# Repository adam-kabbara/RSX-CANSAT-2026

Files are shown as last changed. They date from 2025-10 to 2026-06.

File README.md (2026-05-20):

# RSX CanSat 2T5-2T6 Designs 

<div align="left">
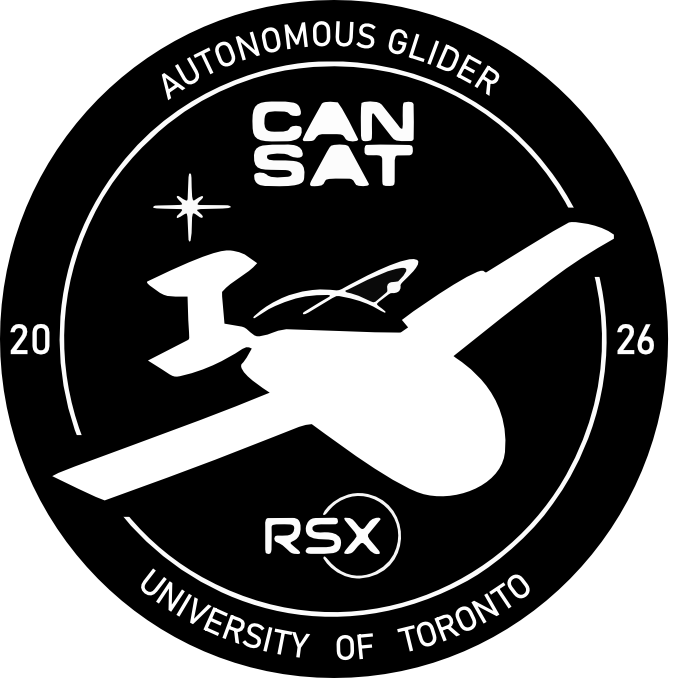
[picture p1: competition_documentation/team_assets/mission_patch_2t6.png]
mission_patch
    
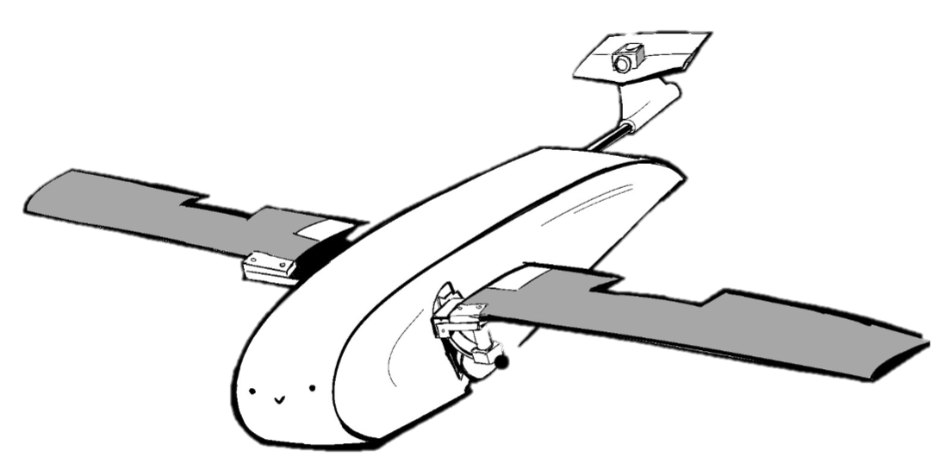
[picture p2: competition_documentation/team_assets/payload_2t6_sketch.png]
payload_sketch
    
    mascot_capybara
</div>
<br>

This repository contains all files created by the Aerial Team of Robotics for Space eXploration (RSX) at the University of Toronto, supporting our entry in the 2026 CanSat Competition.

**Competition Team Members:**
<table align="left">
    <tr><td align="center">Adam Kabbara</td><td align="center">Team Lead</td></tr>
    <tr><td align="center">Arthur Goetzke-Coburn</td><td align="center">Mechanical Team Lead</td></tr>
    <tr><td align="center">Daniel Yu</td><td align="center">Electrical Team Lead</td></tr>
    <tr><td align="center">Luke Watson</td><td align="center">Software Team Lead</td></tr>
    <tr><td align="center">Angelique Liao</td><td align="center">Mechanical Team Member</td></tr>
    <tr><td align="center">Ada Selcuk</td><td align="center">Software Team Member</td></tr>
    <tr><td align="center">Yulin Lin</td><td align="center">Electrical Team Member</td></tr>
    <tr><td align="center">Jingshu Zhu</td><td align="center">Mechanical Team Member</td></tr>
    <tr><td align="center">Vincent Jia</td><td align="center">Mechanical Team Member</td></tr>
    <tr><td align="center">Wareesha Qureshi</td><td align="center">Electrical Team Member</td></tr>
</table>
<br><br><br><br><br><br><br><br><br><br><br><br><br><br><br><br><br>

**Honorary Team Members:**
<table align="left">
    <tr><td align="center">Parth Bhasin</td><td align="center">Electrical Team Member</td></tr>
    <tr><td align="center">John Yfantis</td><td align="center">Electrical Team Member</td></tr>
    <tr><td align="center">Nathan Xia</td><td align="center">Mechanical Team Member</td></tr>
    <tr><td align="center">Gianluca Ceccacci</td><td align="center">Mechanical Team Member</td></tr>
    <tr><td align="center">Berk Yilmaz</td><td align="center">Software Team Member</td></tr>
    <tr><td align="center">Remi Zhang</td><td align="center">Software Team Member</td></tr>
</table>
<br><br><br><br><br><br><br><br><br><br><br>

**CanSat Competition:**
- 📅 June 4-7, 2026
- 📍 Monterey, Virginia, United States
- 🧑‍🚀 [American Astronautical Society (AAS)](https://cansatcompetition.com/winners.html)
- 📃 [Mission Document](CanSat_Mission_Guide_2026g.pdf)

**RSX CanSat 2T4-2T5:**
- 🏆 2025 Competiton Results: [5th Place Internationally](https://cansatcompetition.com/winners.html)
- 💻 GitHub Repo: [RSX-CANSAT-2025](https://github.com/adam-kabbara/RSX-CANSAT-2025)

# 

<p align="center">
    <a href="https://rsx.skule.ca/">
        <picture>
            <source srcset="competition_documentation/team_assets/rsx_logo_dark_mode.svg" media="(prefers-color-scheme: dark)">
            <source srcset="competition_documentation/team_assets/rsx_logo_light_mode.png" media="(prefers-color-scheme: light)">
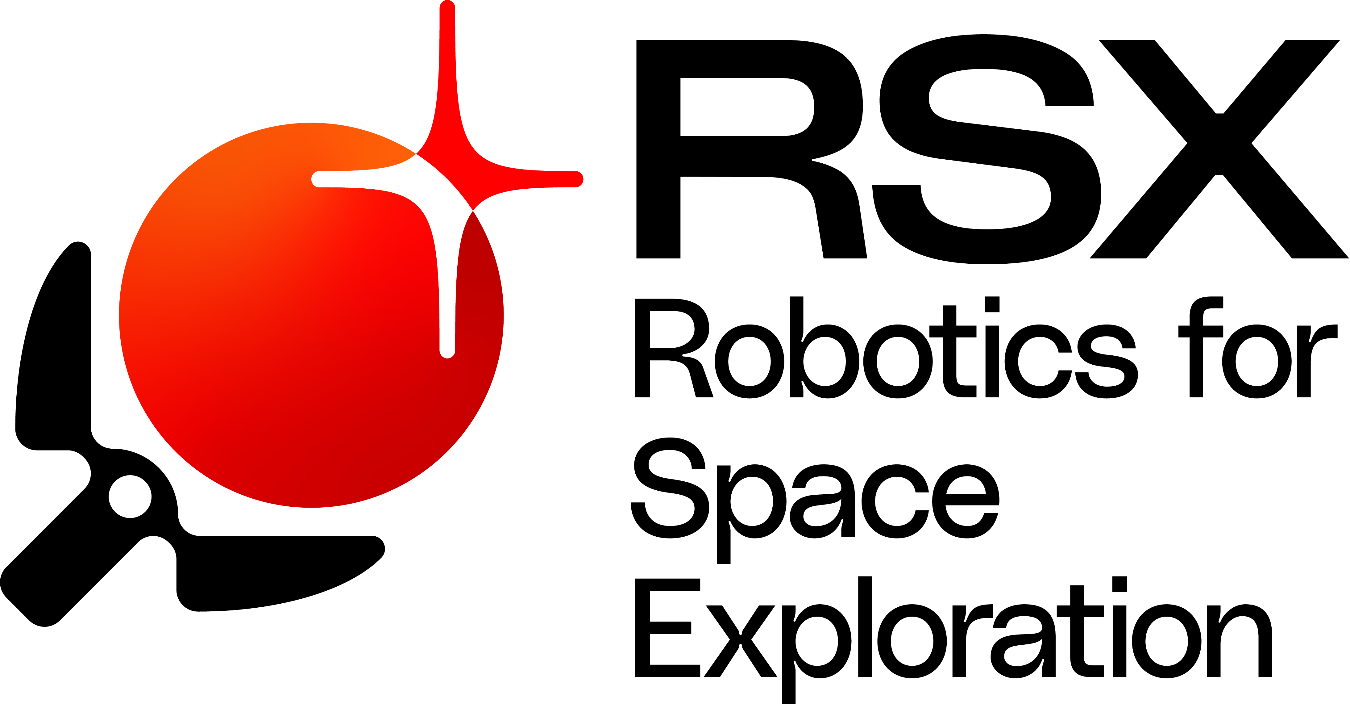
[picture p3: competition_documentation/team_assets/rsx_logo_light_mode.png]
rsx_logo
            
        </picture>
    </a>
</p>
<p align="center">
    <a href="https://www.engineering.utoronto.ca/">
        <picture>
            <source srcset="competition_documentation/team_assets/uoft_engineering_logo_dark_mode.png" media="(prefers-color-scheme: dark)">
            <source srcset="competition_documentation/team_assets/uoft_engineering_logo_light_mode.png" media="(prefers-color-scheme: light)">
            uoft_engineering_logo
        </picture>
    </a>
</p>
<p align="center">
    <a href="https://cansatcompetition.com/">
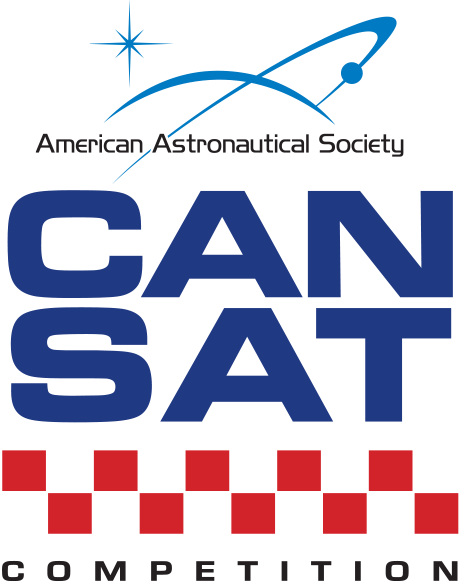
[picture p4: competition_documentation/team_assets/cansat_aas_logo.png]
cansat_aas_logo
        
    </a>
</p>

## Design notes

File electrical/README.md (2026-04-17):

# Datasheets of electronic components
This folder contains datasheets of electronic components used in the project. This readme provides notes and highlights of the datasheets for quick reference.

## MCU
The main MCU used in the project is the Nucleo-32 board with the STM32G4 microcontroller. Datasheet: [STM32G4.pdf](datasheets/um2397-stm32g4-nucleo32-board-mb1430-stmicroelectronics.pdf)

## I2C Adress Book
- INA219 (A0, A1 are gnd on CPL): 0x40
- BMP581: 0x47 (can be changed to 0x46)
- BNO085: 0x4A (can be changed to 0x4B)
- MAXM10S: 0x42 
- VL53L1-SATEL: 0x29

## I/O
### EEPROM
- Datasheet: [EEPROM.pdf](datasheets/EEPROM.pdf)
- Environment: CPL

### INA219
- Datasheet: [ina219.pdf](datasheets/ina219.pdf)
- Environment: Ground station and CPL
- Package: D ; using smd on cpl and adafruit on gnd station

## Power Electronics
### LT8610AB-5
- Datasheet: [LT8610AB-5.pdf](datasheets/LT8610AB.pdf)
- Digikey: [LT8610AB-5](https://www.digikey.com/en/products/detail/analog-devices-inc/LT8610ABEMSE-5-TRPBF/5233264)
- Environment: Ground station
- Details: 5v buck converter from 4s2p (16.8 to 12v) battery to 5v for the ground station. 5 volts used to power the raspberry pi and LED lights. Estimated current consumption to handel is 2.5A.

### LTC3114
- Datasheet: [LTC3114.pdf](datasheets/LTC3114.pdf)
- Digikey: [LTC3114](https://www.digikey.ca/en/products/detail/analog-devices-inc/LTC3114IFE-1-TRPBF/4840586)
- Environment: Ground station
- Details: 12v buckboost from 4s2p (16.8 to 12v) battery to 12v for the ground station. 12 volts used to power the monitor and speakers.
- Package: FE

### LTC3536
- Datasheet: [LTC3536.pdf](datasheets/LTC3536.pdf)
- Digikey: [LTC3536](https://www.digikey.com/en/products/detail/analog-devices-inc/LTC3536EMSE-PBF/2720693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)
- Environment: CPL
- Details: 3.3v buckboost from 1s (3.7v) battery to 3.3v for the sensors on the CPL. 
- Package: MSE

### MP3414
- Datasheet: [MP3414A.pdf](datasheets/MP3414A.pdf)
- Digikey: [MP3414A](https://www.digikey.com/en/products/detail/monolithic-power-systems-inc/MP3414AGJ-Z/7361472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)
- Environment: CPL
- Details: 5.5v boost from 1s (3.7v) battery to 5.5v for the cameras, rtc clock and motors on the CPL.
- Node: To make use of the True Output Disconnect feature, the EN pin must be driven low. So **EN should be connected to Vin**. When battery connected, EN is high and the converter operates. When battery disconnected, EN is low and the converter is disabled and blocks current flow from the output to the input. 

### ~~MAX756CPA+~~
- ~~Datasheet: [max756.pdf](datasheets/max756.pdf)~~
- ~~Environment: CPL~~
- ~~Details: Two exist~~
    - ~~One is for 5v boost from 1s (1.2v) ni-mh battery to 5v for the buzzer circuit on the CPL.~~
    - ~~Another will be used for 5v boost from 1s (3.7v) battery to 5v for the STM on the CPL. This is to allow for power isolation between the STM and the sensors, so we can power the STM without powering the sensors for debugging.~~

- The max startup voltage too low for a NiMh. It does operate down to low voltages, but the startup voltage is higher than what would be reliable for a NiMh battery. Use a MCP1640 for buzzer instead. Can boost to either 5.0V (use NE555) or 3.3v (use TLC555)

### MCP1640
- Datasheet: [MCP1640.pdf](datasheets/MCP1640.pdf)
- Digikey: [MCP1640](https://www.digikey.ca/en/products/detail/microchip-technology/MCP1640T-I-CHY/2258569)
- Environment: CPL buzzer circuit
- Details: replace max756 for 5v boost from 1s (1.2v) ni-mh battery to 5v for the buzzer circuit on the CPL. The MCP1640 has a low startup voltage of 0.65v, which is suitable for a NiMh battery. We will use TLC555 for the oscillator in the buzzer circuit, which can operate at 3.3v instead of NE555.

# TODO LTSPICE BUZZER CICUIT 
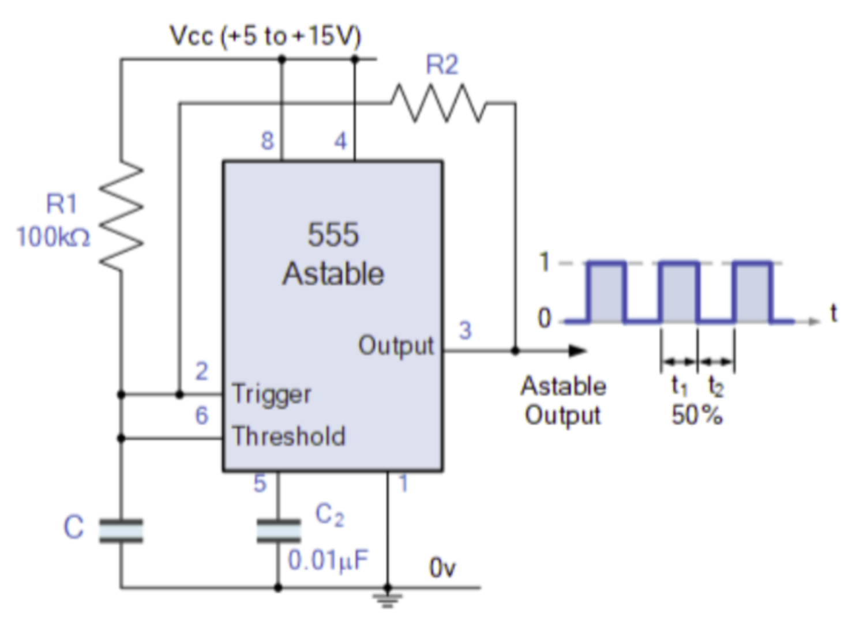
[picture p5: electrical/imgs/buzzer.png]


### Low Voltage Cutoff (LVC) Circuit
The CPL has two low voltage cutoff circuits to ensure the batteries do not over discharge. The two circuits are very similar, but they use slightly different components.

Spice models have been created to simulate these LVCs and can be found in the [Spice folder](Spice/). R1 is just there to model our load. In the actual circuit, we will have that node connected to the Vin of our voltage converters.

1. Main battery ([21700 Li-ion](https://rotorgeeks.com/samsung-50e-5000mah-98a-21700-cell)) LVC:
    - Supervisor: [TPS3839K33](https://www.digikey.ca/en/products/detail/texas-instruments/TPS3839K33DBZR/3748986)
    - Inverter: [SN74LVC1G04](https://www.digikey.ca/en/products/detail/umw/SN74LVC1G04DBVR/16842214)
    - PMOSFET: [SI4435DDY](https://www.digikey.ca/en/products/detail/vishay-siliconix/SI4435DDY-T1-E3/2622193)
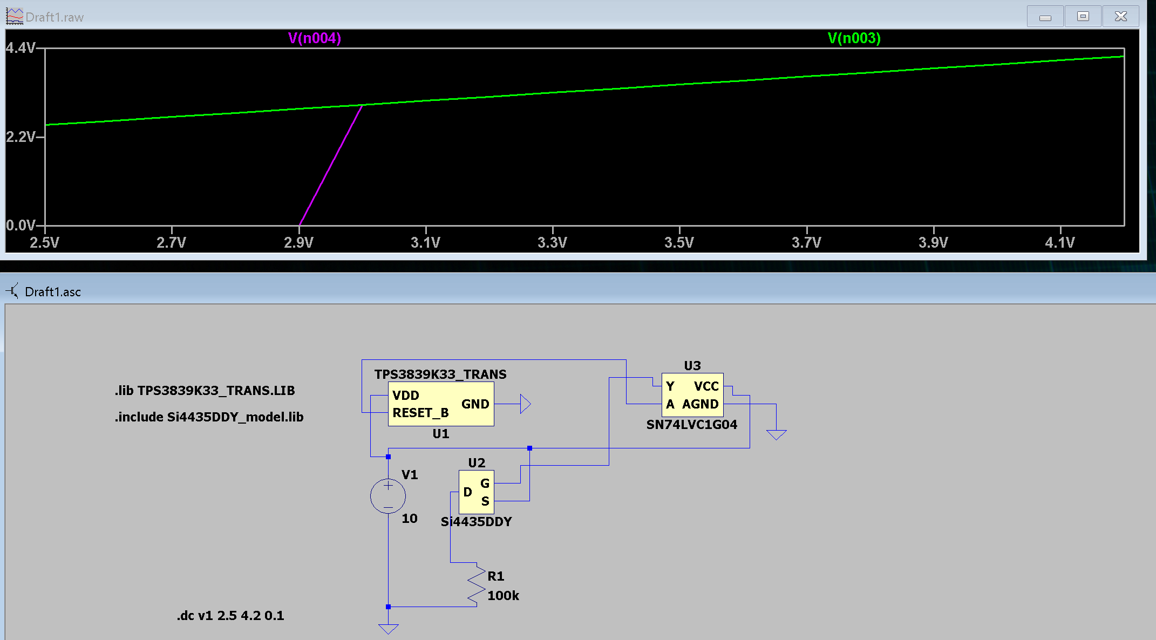
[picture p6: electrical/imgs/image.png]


2. Buzzer battery ([Ni-MH](https://www.digikey.ca/en/products/detail/panasonic-energy/HHR-70AAAE4/597940)) LVC:
    - Supervisor: [TPS3839A09DBZR](https://www.digikey.ca/en/products/detail/texas-instruments/TPS3839A09DBZR/3900178)
    - Inverter: [SN74AUP1G04](https://www.digikey.ca/en/products/detail/texas-instruments/SN74AUP1G04DBVR/864075)
    - PMOSFET: [SI4435DDY](https://www.digikey.ca/en/products/detail/vishay-siliconix/SI4435DDY-T1-E3/2622193)

### Battery Info
As mentioned in the section above, we have two rechargable batteries on the CPL, a [samsung 50e 21700 li-ion](https://rotorgeeks.com/samsung-50e-5000mah-98a-21700-cell) as the main battery, and a [panasonic HHR-70AAAE4 ni-mh](https://www.digikey.ca/en/products/detail/panasonic-energy/HHR-70AAAE4/597940) as the buzzer battery. Below are some important notes about these batteries.
#### Samsung 50e 21700 Li-ion
- Datasheet: [samsung_50e.pdf](datasheets/samsung_50e.pdf)
- **Charge at 2450mA (~0.5C) at 4.2v**
- Nominal voltage: 3.63v
- Max voltage: 4.2v
- Min voltage: 3.0 (defined by us - technically can go down to 2.5v)
- Capacity: 5000mAh
#### Panasonic HHR-70AAAE4 Ni-MH
- Datasheet: [panasonic_hhr.pdf](datasheets/panasonic_hhr.pdf)
- **Standard charge at 70mA at 1.4v**
- **Rapid charge at 650mA at 1.4v**
- Nominal voltage: 1.2v
- Max voltage: 1.4v
- Min voltage: 1.1v (defined by us - technically can go down to ~<0.9v)
- Capacity: 700mAh
---

### General Notes
#### Power Isolation
To allow for debugging, the STM32 must be able to be powered without powering the sensors. To achieve this, we decide put the STM on a separate power rail from the sensors, so it will need a seperate boost (5v power option) or buckboost (3.3v power option) converter. We decide to go with 3.3v as we have an extra LTC3536 buckboost converter, which will be used to power the STM alone. To allow for debugging though, the sensors (and motors) must also be able to be powered without powering the STM. We need power isolation between all output rails. 

**We will assume that debugging always happens when the battery is disconnected (and has been for a couple seconds), the battery + and - terminals are grounded. Power is supplied to the stm32, sensors and motors at the Vout nodes of the stm_3.3v, 3.3v, and 5.5v converters via the test points.** 

No voltage should be present at the Vin terminals of the converters this **WILL** break stuff. So do not connect power to where the battery was connected, you must provide power to the sensors and motors using an external power supply connected to the test points on the PCB.

Below is the thought process for the power isolation design.

**MP3414A**:
- Synchronous boost with true output disconnect via internal PMOS. Actively blocks body diode conduction in shutdown according to datasheet.
- For this to work **EN must be tied to Vin**, that way when Vin is disconnected from the battery, EN is low and the converter is disabled and blocks current flow from the output to the input. When battery is connected, EN is high and the converter operates as normal.

**LTC3536**:
- 4-switch synchronous buck-boost with a direct reverse path while running
- If EN is high while Vout was driven, it has a reverse current limit (0.55A) to protect itself, but doesn't fully prevent backflow. We should NOT rely on this feature to prevent backflow, we should make sure converter is disabled when battery is disconnected.
- SHDN (shutdown) pin is active-high, so **tie SHDN to VIN**. Allows converter to operate when battery is connected, and disables it when battery is disconnected while preverting backflow.

**Max756CPA+**:
- Asynchronous boost with external discrete 1N5822 Schottky
- Schottky provides hard reverse blocking
- Reverse current at our expected voltage and temperatures is negligible.
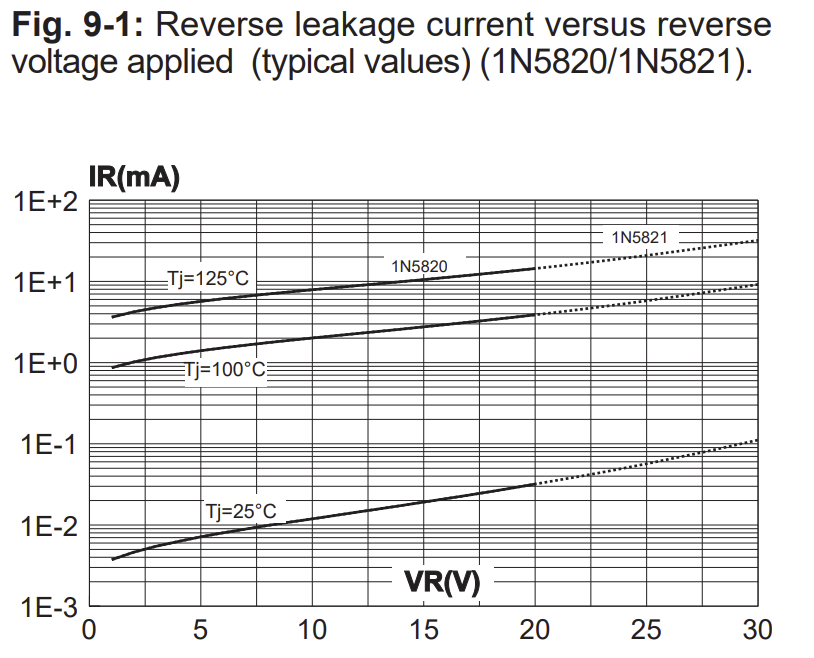
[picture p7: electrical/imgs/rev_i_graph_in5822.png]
 

To ensure Vin is truely discharged while debugging, we will add a solder bridge across, from Vin to a pull down resistor to GND. This resistor must be a through hole (estimated value of 3.3kΩ) to ensure fast discharge of Vin when battery is disconnected. This will mean we will lose some current through the resistor, we may have to tune this value. **The solder bridge must only be connected while testing, it should be disconnected during normal operation.**

---

#### Board debugging procedure
Debugging is defined as powering the STM32 with an external power supply while the battery is disconnected, to allow for debugging without powering the sensors. ~~You can perfrom debugging with either the stm_3.3v being supplied alone (just programming the stm32) or with all stm_3.3v, 3.3v, and 5.5v being supplied (programming while also having sensors, motors and cameras running).~~

~~Follow the steps below **in order** to ensure the power isolation features work as intended and nothing gets damaged. If you just want to program the STM without powering the other components skip steps 4-5.~~
<del>
    1. Disconnect battery ensuring Vin is pulled to ground (both battery terminals are grounded)
    2. Using a multimeter, verify that there is no voltage at the Vin terminals of the converters.
    3. Ensure the solder bridge sb15 is disconnected
    4. Provide power to the sensors via external power supply connected to the 3.3v and GND test point on the PCB.
    5. Provide power to the motors and cameras via external power supply connected to the 5.5v and GND test point on the PCB.
    6. Provide power to the STM via external power supply connected to the stm_3.3v and GND test point on the PCB.
    7. Ensure all grounds are common
    8. Now you can move to STM debugging setup sequence (step 4 below)
</del>

The above proceedure is outdated. It was for when stm and sensors were on the same power rail. And then was slightly modified for when they were on different rails. 

But apon reflection, the power isolation features should be robust enough to allow for the following simplified debugging proceedure.
1. Ensure the solder bridge sb15 is disconnected
2. Connect battery or power supply (3.6v) to the battery terminals.
3. All power rails should be on, and all systems should be active.
4. You can now debug the STM32 by simply plugging in the USB into the nucleo board.

The STM must follow this specific power up sequence. This proceedure was develpoed with the help of the STM32 docs below.
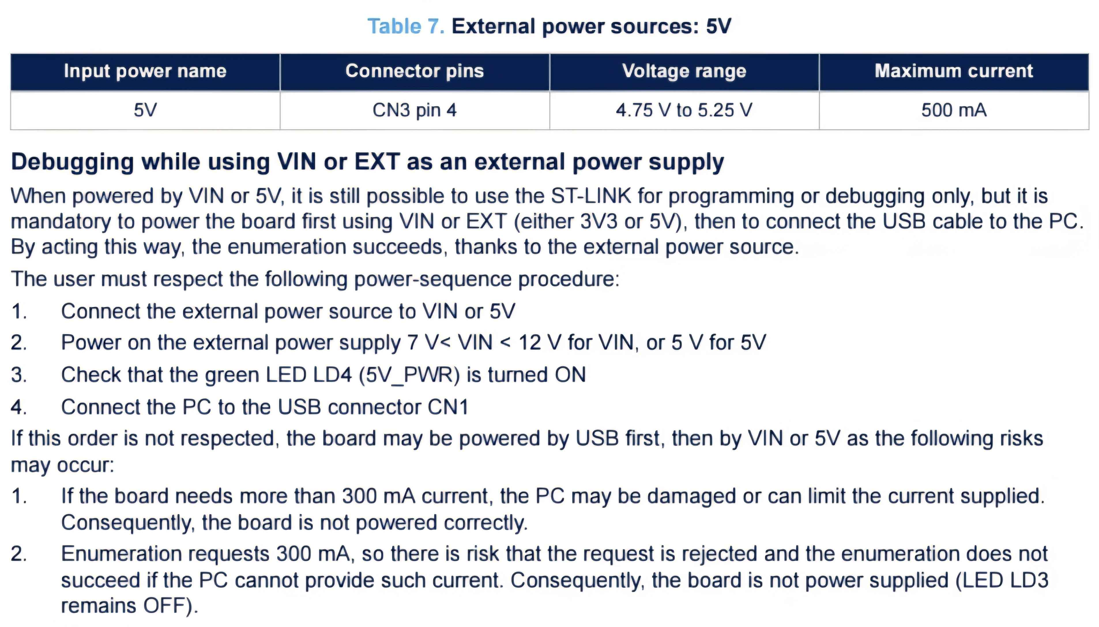
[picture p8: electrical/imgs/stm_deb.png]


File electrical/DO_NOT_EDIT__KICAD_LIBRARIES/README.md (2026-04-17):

# ⚠️ DO NOT EDIT THIS FOLDER! | KiCad Custom Models

<p align="center">
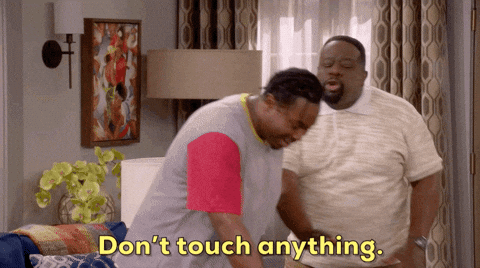
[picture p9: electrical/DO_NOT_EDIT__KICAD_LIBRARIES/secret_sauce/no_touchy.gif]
No Touchy!
  
</p>

### Please do not edit any of these files! They are linked to the Electrical Team's KiCad library setups and any edits will break the custom component connections on our PCB designs.

### If any updates are required, please make sure to let [@danielz-yu](https://github.com/danielz-yu) know and push those change on the [kicad_custom_updates](https://github.com/adam-kabbara/RSX-CANSAT-2026/tree/kicad_custom_updates) branch.

### Download Steps:
1. 📥 `git pull origin main` to update the [symbols](https://github.com/adam-kabbara/RSX-CANSAT-2026/tree/main/electrical/DO_NOT_EDIT__KICAD_LIBRARIES/symbols) and [footprints](https://github.com/adam-kabbara/RSX-CANSAT-2026/tree/main/electrical/DO_NOT_EDIT__KICAD_LIBRARIES/footprints) folders.
2. 🛠️ Open *KiCad Symbol Editor* --> Preferences --> Manage Symbol Libraries --> Folder Icon (bottom left corner) --> Select the *symbols* folder at the path listed below --> Press *OK*.
3. 🛠️ Open *KiCad Footprint Editor* --> Preferences --> Manage Footprint Libraries --> Folder Icon (bottom left corner) --> Select the *.pretty* files at the paths listed below --> Press *OK*.
4. 🛠️ TBA for 3D Models.

 ### Symbols:
- ✅ __Active__
- ✅ __Visible__
- __🏷️ Nickname:__ RSX_CanSat_Custom_KiCad_Symbols
- __🗂️ Path:__ /{USER_PATH}/RSX-CANSAT-2026/electrical/DO_NOT_EDIT__KICAD_LIBRARIES/symbols/RSX_CanSat_Custom_KiCad_Symbols.kicad_sym
- __📝 Description:__ RSX Aerial CanSat Custom KiCad Symbols

### Footprints:
- **Sensor Footprints**
    - ✅ __Active__
    - ✅ __Visible__
    - __🏷️ Nickname:__ RSX_CanSat_Custom_KiCad_Footprints
    - __🗂️ Path:__ /{USER_PATH}/RSX-CANSAT-2026/electrical/DO_NOT_EDIT__KICAD_LIBRARIES/footprints/RSX_CanSat_Custom_KiCad_Footprints.pretty
    - __📝 Description:__ RSX Aerial CanSat Custom KiCad Footprints
- **Silkscreen Graphics**
    - ✅ __Active__
    - ✅ __Visible__
    - __🏷️ Nickname:__ RSX_CanSat_Graphics
    - __🗂️ Path:__ /{USER_PATH}/RSX-CANSAT-2026/electrical/DO_NOT_EDIT__KICAD_LIBRARIES/footprints/RSX_CanSat_Graphics.pretty
    - __📝 Description:__ RSX Aerial CanSat Custom KiCad Graphics

### 3D Models:
- TBA
- Preferences>Configure Paths
- Click plus btn, add "CUSTOM_3D_MODELS" as a name and /{USER_PATH}/RSX-CANSAT-2026/electrical/DO_NOT_EDIT__KICAD_LIBRARIES/Custom_3D_Models.3dshapes as the path

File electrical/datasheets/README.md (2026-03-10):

@adamlkabbara to fix this 

# Datasheets of electronic components
This folder contains datasheets of electronic components used in the project. This readme provides notes and highlights of the datasheets for quick reference.

## I2C Adress Book
- INA219 (A0, A1 are gnd on CPL): 0x40
- BMP581: 0x47 (can be changed to 0x46)
- BNO085: 0x4A (can be changed to 0x4B)
- MAXM10S: 0x42 
- VL53L1-SATEL: 0x29

## I/O
### EEPROM
- Datasheet: [EEPROM.pdf](EEPROM.pdf)
- Environment: CPL

### INA219
- Datasheet: [ina219.pdf](ina219.pdf)
- Environment: Ground station and CPL
- Package: D ; using smd on cpl and adafruit on gnd station

## Power Electronics
### LT8610AB
- Datasheet: [LT8610AB.pdf](LT8610AB.pdf)
- Environment: Ground station
- Details: 5v buck converter from 4s2p (16.8 to 12v) battery to 5v for the ground station. 5 volts used to power the raspberry pi and LED lights. Estimated current consumption to handel is 2.5A.

### LTC3114
- Datasheet: [LTC3114.pdf](LTC3114.pdf)
- Environment: Ground station
- Details: 12v buckboost from 4s2p (16.8 to 12v) battery to 12v for the ground station. 12 volts used to power the monitor and speakers.
- Package: FE

### LTC3536
- Datasheet: [LTC3536.pdf](LTC3536.pdf)
- Digikey: [LTC3536](https://www.digikey.com/en/products/detail/analog-devices-inc/LTC3536EMSE-PBF/2720693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)
- Environment: CPL
- Details: 3.3v buckboost from 1s (3.7v) battery to 3.3v for the sensors on the CPL. 

### MP3424
- Datasheet: [MP3424A.pdf](MP3424A.pdf)
- Digikey: [MP3424A](https://www.digikey.com/en/products/detail/monolithic-power-systems-inc/MP3414AGJ-Z/7361472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)
- Environment: CPL
- Details: 5.5v boost from 1s (3.7v) battery to 5.5v for the cameras, rtc clock and motors on the CPL.
- Node: To make use of the True Output Disconnect feature, the EN pin must be driven low. So **EN should be connected to Vin**. When battery connected, EN is high and the converter operates. When battery disconnected, EN is low and the converter is disabled and blocks current flow from the output to the input. 

### MAX756CPA+
- Datasheet: [max756.pdf](max756.pdf)
- Environment: CPL
- Details: 5v boost from 1s (1.2v) ni-mh battery to 5v for the buzzer circuit on the CPL.

---

### General Notes
#### Power Isolation
To allow for debugging, the STM32 must be able to be powered without powering the sensors. To achieve this, we decide put the STM on a separate power rail from the sensors, so it will need a seperate boost (5v power option) or buckboost (3.3v power option) converter. We decide to go with 5v as we have an extra Max756CPA+ boost converter, which will be used to power the STM alone. To allow for debugging though, the sensors (and motors) must also be able to be powered without powering the STM. We need power isolation between all output rails. 

**We will assume that debugging always happens when the battery is disconnected (and has been for a couple seconds) and power is supplied to the stm through the usb, while power is supplied to the sensors and motors at the Vout nodes of the 3.3v and 5.5v converters.** 

No voltage should be present at the Vin terminals of the converters this **WILL** break stuff. So do not connect power to where the battery was connected, you must provide power to the sensors and motors using an external power supply connected to the test points on the PCB.

Below is the thought process for the power isolation design.

**MP3424A**:
- Synchronous boost with true output disconnect via internal PMOS. Actively blocks body diode conduction in shutdown according to datasheet.
- For this to work **EN must be tied to Vin**, that way when Vin is disconnected from the battery, EN is low and the converter is disabled and blocks current flow from the output to the input. When battery is connected, EN is high and the converter operates as normal.

**LTC3536**:
- 4-switch synchronous buck-boost with a direct reverse path while running
- If EN is high while Vout was driven, it has a reverse current limit (0.55A) to protect itself, but doesn't fully prevent backflow. We should NOT rely on this feature to prevent backflow, we should make sure converter is disabled when battery is disconnected.
- SHDN (shutdown) pin is active-high, so **tie SHDN to VIN**. Allows converter to operate when battery is connected, and disables it when battery is disconnected while preverting backflow.

**Max756CPA+**:
- Asynchronous boost with external discrete 1N5822 Schottky
- Schottky provides hard reverse blocking
- Reverse current at our expected voltage and temperatures is negligible.
 

To ensure Vin is truely discharged while debugging, we will add a solder bridge across, from Vin to a pull down resistor to GND. This resistor must be a through hole (estimated value of 3.3kΩ) to ensure fast discharge of Vin when battery is disconnected. This will mean we will lose some current through the resistor, we may have to tune this value. **The solder bridge must only be connected while testing, it should be disconnected during normal operation.**

---

#### Board debugging procedure
There are two actors that require processing before board debugging. Follow in the order below:
1. Power isolation must be ensured as discussed in the previous section. To do this:
    - Disconnect battery and connect the solder bridge, ensuring Vin is pulled to ground through the pull down resistor.
    - Using a multimeter, verify that there is no voltage at the Vin terminals of the converters.
    - Provide power to the sensors via external power supply connected to the 3.3v and GND test point on the PCB.
    - Provide power to the motors and cameras via external power supply connected to the 5.5v and GND test point on the PCB.
    - Provide power to the STM via external power supply connected to the 5v and GND test point on the PCB. 
    - Now you can move to STM debugging setup sequence.
2. The STM must follow a specific power up sequence.


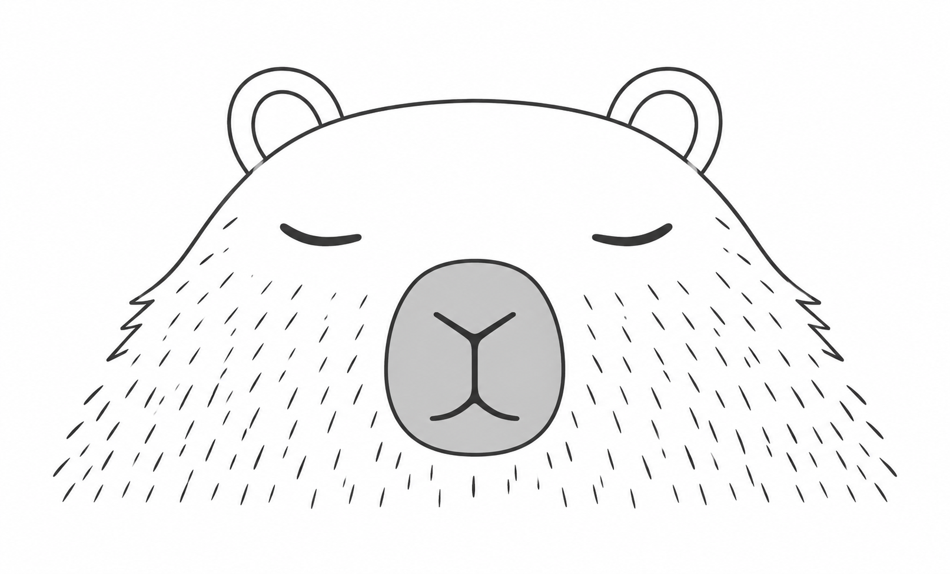
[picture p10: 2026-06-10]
mechanical/gnd_station/art/ChatGPT Image May 14, 2026, 07_00_57 AM.png

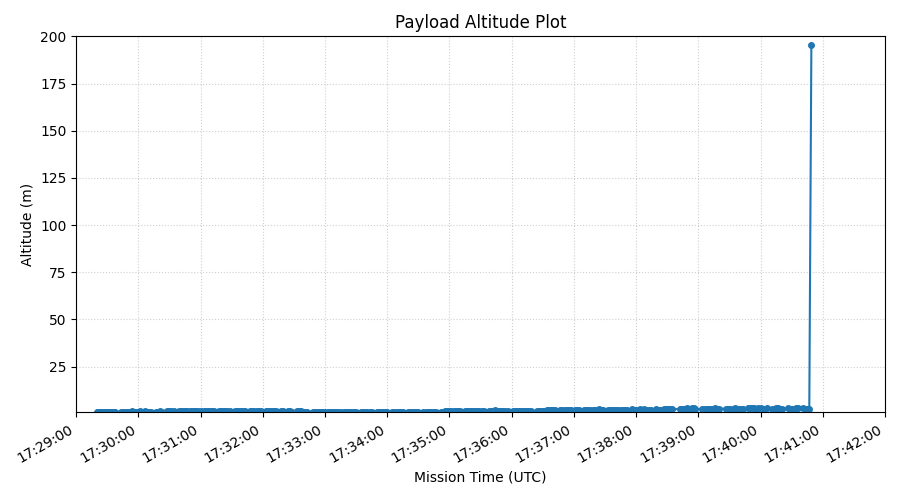
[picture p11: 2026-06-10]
pfr_analysis/graphs/altitude.png

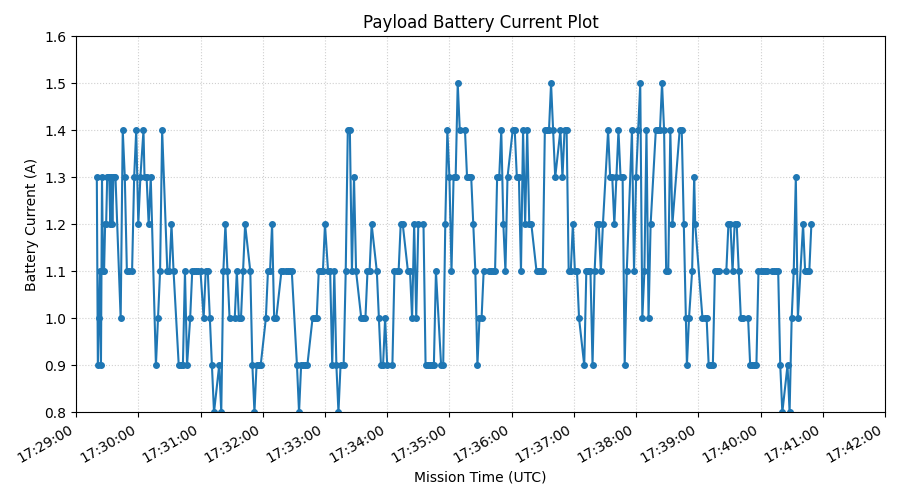
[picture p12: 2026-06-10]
pfr_analysis/graphs/current.png

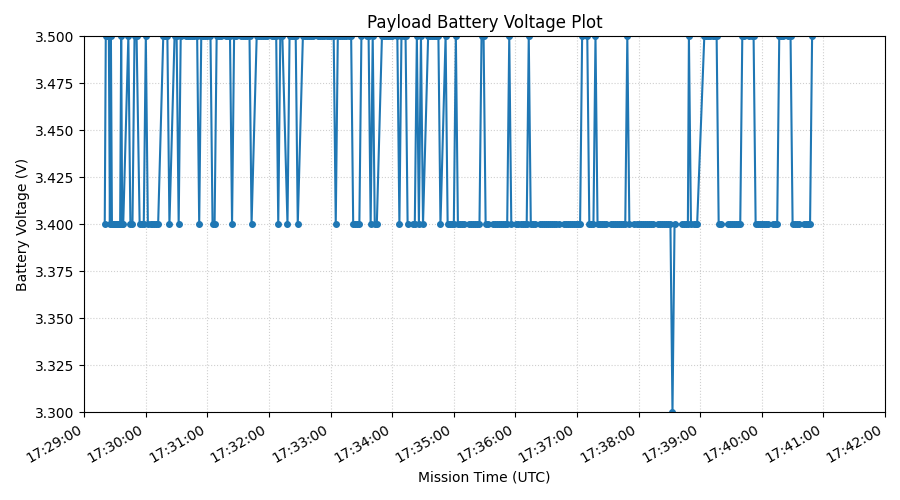
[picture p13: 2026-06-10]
pfr_analysis/graphs/voltage.png

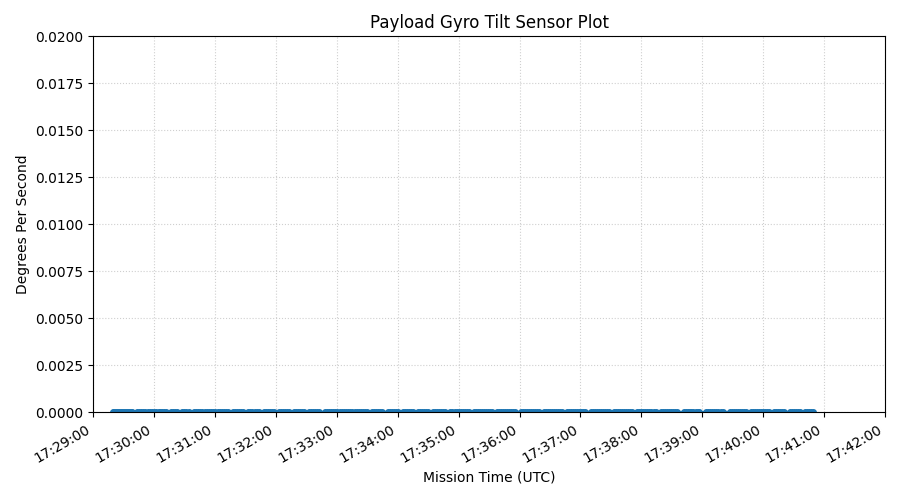
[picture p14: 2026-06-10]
pfr_analysis/graphs/gyro.png

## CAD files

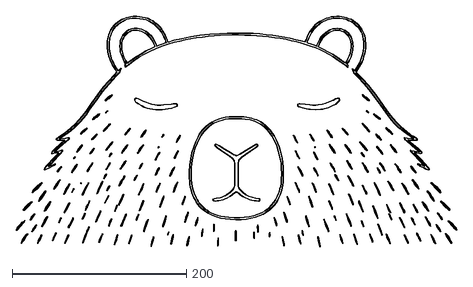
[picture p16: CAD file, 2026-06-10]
mechanical/gnd_station/art/yes_hair_capy.dxf
505.4 x 264.2

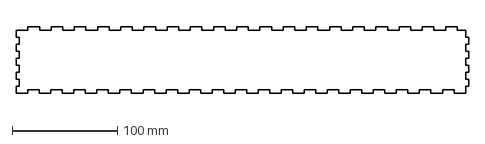
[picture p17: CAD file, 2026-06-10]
mechanical/gnd_station/DXFs/gs_base/back_outer.dxf
430.0 x 63.0 mm

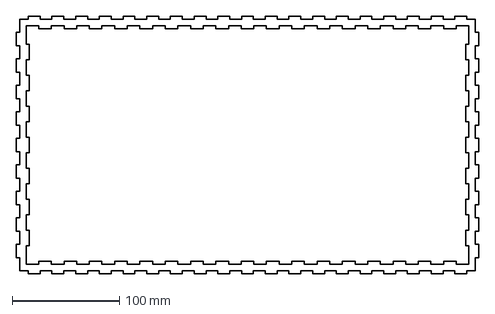
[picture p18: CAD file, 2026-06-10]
mechanical/gnd_station/DXFs/gs_cover/front.dxf
430.0 x 240.0 mm

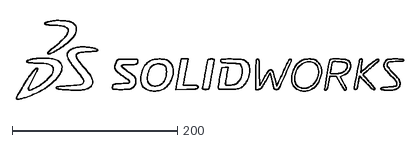
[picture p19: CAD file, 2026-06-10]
mechanical/gnd_station/sponsor logos/dfx-ed/ImageToStl.com_solidworks.dxf
469.4 x 95.9

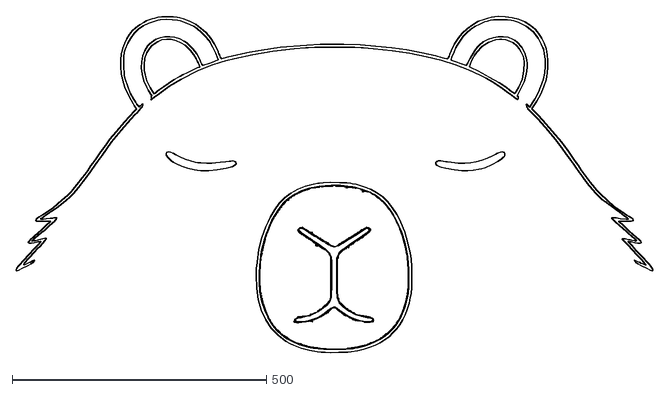
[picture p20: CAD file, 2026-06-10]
mechanical/gnd_station/sponsor logos/from_rsx_drive/adam_svg/ImageToStl.com_ChatGPT+Image+May+14,+2026,+07_00_57+AM.dxf
1251.6 x 660.5

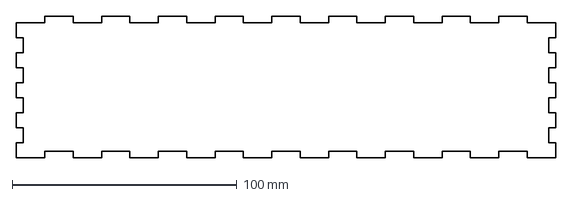
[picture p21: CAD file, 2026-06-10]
mechanical/gnd_station/DXFs/gs_base/left_outer.dxf
240.0 x 63.0 mm

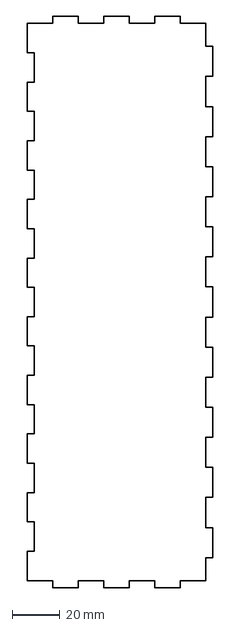
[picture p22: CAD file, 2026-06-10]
mechanical/gnd_station/DXFs/gs_cover/right_outer.dxf
78.0 x 240.0 mm

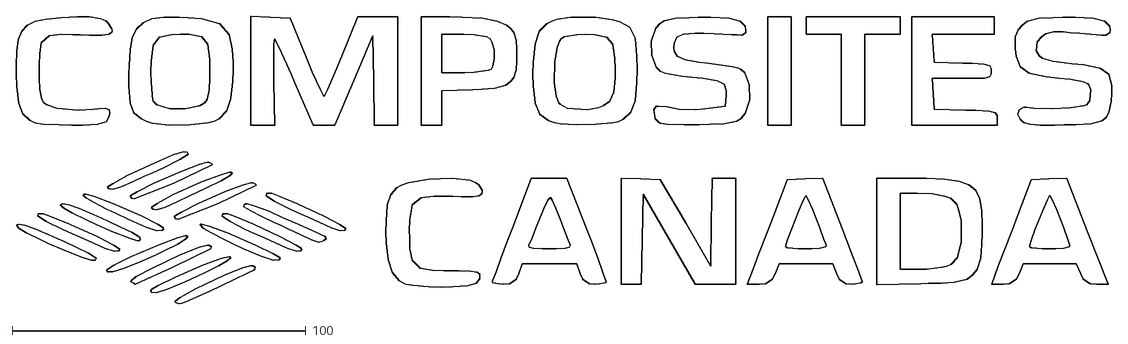
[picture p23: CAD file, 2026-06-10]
mechanical/gnd_station/sponsor logos/dfx-ed/CompositesCanadaLogo.dxf
372.8 x 97.7

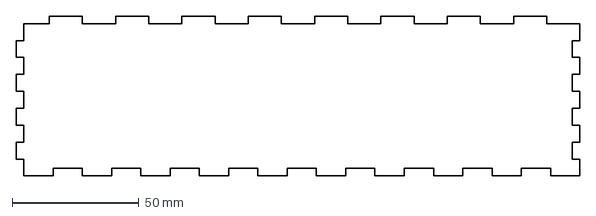
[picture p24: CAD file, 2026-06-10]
mechanical/gnd_station/DXFs/gs_base/right_inner.dxf
222.0 x 63.0 mm

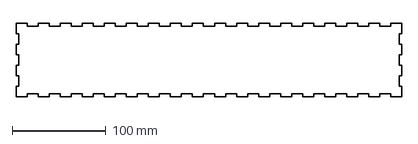
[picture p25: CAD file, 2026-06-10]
mechanical/gnd_station/DXFs/gs_cover/top_inner.dxf
412.0 x 78.0 mm

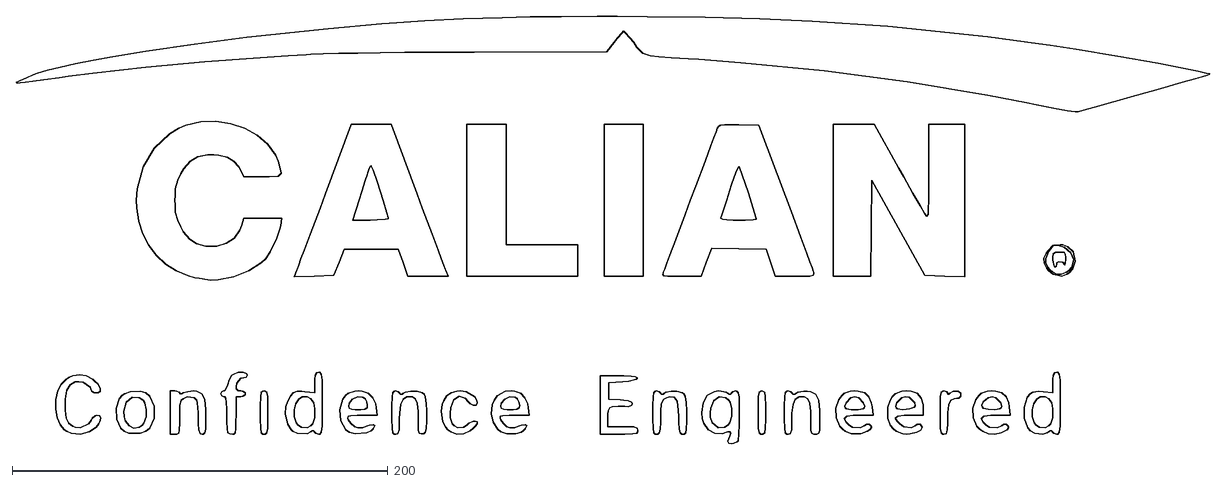
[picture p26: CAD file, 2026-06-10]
mechanical/gnd_station/sponsor logos/dfx-ed/calian.dxf
635.7 x 227.4

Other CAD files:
mechanical/gnd_station/DWGs/architecture_building_lazer_cutter/pls_boundary_812mm_by_457mm.dwg
mechanical/gnd_station/DWGs/gs_base_outer.dwg
mechanical/gnd_station/DWGs/architecture_building_lazer_cutter/ils_boundary_1219mm_by_609mm.dwg
mechanical/gnd_station/DWGs/gs_base_inner.dwg
mechanical/gnd_station/DWGs/gs_top_inner.dwg
mechanical/gnd_station/DWGs/gs_top_outer.dwg
mechanical/gnd_station/DXFs/gs_base/back_inner.dxf
mechanical/gnd_station/DXFs/gs_base/bottom.dxf
mechanical/gnd_station/DXFs/gs_base/front_inner.dxf
mechanical/gnd_station/DXFs/gs_base/front_outer.dxf
mechanical/gnd_station/DXFs/gs_base/left_inner.dxf
mechanical/gnd_station/DXFs/gs_base/right_outer.dxf
mechanical/gnd_station/DXFs/gs_base/top.dxf
mechanical/gnd_station/DXFs/gs_cover/back.dxf
mechanical/gnd_station/DXFs/gs_cover/bottom_inner.dxf
mechanical/gnd_station/DXFs/gs_cover/bottom_outer.dxf
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

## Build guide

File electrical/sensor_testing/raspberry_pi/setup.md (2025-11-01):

## Raspberry Pi Zero W Connection Guide
1. Ensure to connect your computer to the `rsx_base_router2` network.
2. Open CMD and type `ssh pi@192.168.0.110`. The password is the same password as the wifi

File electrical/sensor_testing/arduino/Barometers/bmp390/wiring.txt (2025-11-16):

Connect Vin to the power supply, 3-5V is fine. (Red
wire on STEMMA QT version.) Use the same
voltage that the microcontroller logic is based off
of. For most older Arduinos, that is 5V.
Connect GND to common power/data
ground. (Black wire on STEMMA QT version.)
Connect the SCK/SCL pin to the 12C clock SCL pin
on your Arduino. (Yellow wire on STEMMA QT
version.) On an UNO & '328 based Arduino, this is
also known as A5, on a Mega it is also known as
digital 21 and on a Leonardo/Micro, digital 3.
Connect the SDI/SDA pin to the 12C data SDA pin
on your Arduino. (Blue wire on STEMMA QT
version.) On an UNO & '328 based Arduino, this is
also known as A4, on a Mega it is also known as
digital 20 and on a Leonardo/Micro, digital 2.

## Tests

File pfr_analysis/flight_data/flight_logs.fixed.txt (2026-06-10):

$LOGFILE:BEGIN
1011,03:24:24,1,F,LAUNCH_PAD,0.8,40.6,92.4,3.4,1.3,0,0,0,0,0,0,17:29:20,820.6,38.3756,-79.6075,12,CXON,-0.0,0.0,-0.0,0.0,0.0,0.0,-0.0,0.0,-0.0
1011,03:24:25,2,F,LAUNCH_PAD,0.9,40.6,92.4,3.5,0.9,0,0,0,-2147483648,0,2147483647,17:29:21,820.7,38.3756,-79.6075,12,CXON,-0.0,0.0,-0.0,0.0,0.0,0.0,-0.0,0.0,-0.0
1011,03:24:26,3,F,LAUNCH_PAD,0.8,40.6,92.4,3.5,1.0,0,0,0,0,0,0,17:29:22,820.7,38.3756,-79.6075,12,CXON,-0.0,0.0,-0.0,0.0,0.0,0.0,-0.0,0.0,-0.0
1011,03:24:27,4,F,LAUNCH_PAD,0.7,40.6,92.4,3.5,1.1,0,0,0,0,0,0,17:29:23,820.7,38.3756,-79.6075,12,CXON,-0.0,0.0,-0.0,0.0,0.0,0.0,-0.0,0.0,-0.0
1011,03:24:28,5,F,LAUNCH_PAD,0.8,40.6,92.4,3.5,0.9,0,0,0,0,0,0,17:29:24,820.7,38.3756,-79.6075,12,CXON,-0.0,0.0,-0.0,0.0,0.0,0.0,-0.0,0.0,-0.0
1011,03:24:29,6,F,LAUNCH_PAD,0.8,40.6,92.4,3.4,1.3,0,0,0,0,0,0,17:29:25,820.6,38.3756,-79.6075,12,CXON,-0.0,0.0,-0.0,0.0,0.0,0.0,-0.0,0.0,-0.0
1011,03:24:30,7,F,LAUNCH_PAD,0.8,40.6,92.4,3.5,1.1,0,0,0,0,0,0,17:29:26,820.5,38.3756,-79.6075,12,CXON,-0.0,0.0,-0.0,0.0,0.0,0.0,-0.0,0.0,-0.0
1011,03:24:31,8,F,LAUNCH_PAD,0.8,40.6,92.4,3.4,1.1,0,0,0,0,0,0,17:29:27,820.3,38.3756,-79.6075,12,CXON,-0.0,0.0,-0.0,0.0,0.0,0.0,-0.0,0.0,-0.0
1011,03:24:32,9,F,LAUNCH_PAD,0.8,40.6,92.4,3.4,1.2,0,0,0,0,0,0,17:29:28,820.1,38.3756,-79.6075,12,CXON,-0.0,0.0,-0.0,0.0,0.0,0.0,-0.0,0.0,-0.0
1011,03:24:33,10,F,LAUNCH_PAD,0.8,40.6,92.4,3.4,1.2,0,0,0,0,0,0,17:29:29,819.9,38.3756,-79.6075,12,CXON,-0.0,0.0,-0.0,0.0,0.0,0.0,-0.0,0.0,-0.0
1011,03:24:34,11,F,LAUNCH_PAD,0.9,40.6,92.4,3.4,1.3,0,0,0,0,0,0,17:29:30,819.7,38.3756,-79.6075,12,CXON,-0.0,0.0,-0.0,0.0,0.0,0.0,-0.0,0.0,-0.0
1011,03:24:35,12,F,LAUNCH_PAD,0.8,40.6,92.4,3.4,1.3,0,0,0,0,0,0,17:29:31,819.6,38.3756,-79.6075,12,CXON,-0.0,0.0,-0.0,0.0,0.0,0.0,-0.0,0.0,-0.0
1011,03:24:36,13,F,LAUNCH_PAD,0.9,40.6,92.4,3.4,1.3,0,0,0,0,0,0,17:29:32,819.5,38.3756,-79.6075,12,CXON,-0.0,0.0,-0.0,0.0,0.0,0.0,-0.0,0.0,-0.0
1011,03:24:37,14,F,LAUNCH_PAD,0.9,40.6,92.4,3.4,1.2,0,0,0,0,0,0,17:29:33,819.4,38.3756,-79.6075,12,CXON,-0.0,0.0,-0.0,0.0,0.0,0.0,-0.0,0.0,-0.0
1011,03:24:38,15,F,LAUNCH_PAD,0.8,40.6,92.4,3.4,1.3,0,0,0,0,0,0,17:29:34,819.3,38.3756,-79.6075,12,CXON,-0.0,0.0,-0.0,0.0,0.0,0.0,-0.0,0.0,-0.0
1011,03:24:39,16,F,LAUNCH_PAD,0.9,40.6,92.4,3.4,1.2,0,0,0,0,0,0,17:29:35,819.2,38.3756,-79.6075,12,CXON,-0.0,0.0,-0.0,0.0,0.0,0.0,-0.0,0.0,-0.0
1011,03:24:40,17,F,LAUNCH_PAD,0.8,40.6,92.4,3.5,1.3,0,0,0,0,0,0,17:29:36,819.1,38.3756,-79.6075,12,CXON,-0.0,0.0,-0.0,0.0,0.0,0.0,-0.0,0.0,-0.0
1011,03:24:41,18,F,LAUNCH_PAD,0.8,40.6,92.4,3.4,1.3,0,0,0,0,0,0,17:29:37,819.1,38.3756,-79.6075,12,CXON,-0.0,0.0,-0.0,0.0,0.0,0.0,-0.0,0.0,-0.0
1011,03:24:42,19,F,LAUNCH_PAD,1.0,40.6,92.4,3.4,1.3,0,0,0,0,0,0,17:29:38,819.0,38.3756,-79.6075,12,CXON,-0.0,0.0,-0.0,0.0,0.0,0.0,-0.0,0.0,-0.0
1011,03:24:43,20,F,LAUNCH_PAD,1.0,40.7,92.4,3.4,1.4,0,0,0,0,0,0,17:29:
1011,03:24:44,21,F,LAUNCH_PAD,1.0,40.6,92.4,3.4,1.4,0,0,0,0,0,0,:40,819.0,38.3756,-79.6075,12,CXON,-0.0,0.0,-0.0,0.0,0.0,0.0,-0.
1011,03:24:45,22,F,LAUNCH_PAD,1.0,40.7,92.4,3.5,1.1,0,0,0,0,0,0,
1011,03:24:46,23,F,LAUNCH_PAD,1.0,40.6,92.4,3.4,1.4,0,0,0,0,0,0,0,0.0,0.0,0.0,-0.0,0.0,-0.0
1011,03:24:47,24,F,LAUNCH_PAD,1.1,40.7,92.4,3.5,1.0,0,0,0,0,0,0,17:29:43,819.3,38.3756,-79.6075,12,C
1011,03:24:48,25,F,LAUNCH_PAD,1.0,40.7,92.4,3.5,1.1,0,0,0,0,0,0,
1011,03:24:49,26,F,LAUNCH_PAD,1.0,40.7,92.4,3.4,1.4,0,0,0,0,0,0,17:29:45,819.8,38.3756,-79.6075,12,CXON,-0.0,0.0,-0.0,0.0,0.0,0.
1011,03:24:50,27,F,LAUNCH_PAD,1.0,40.7,92.4,3.5,1.1,0,0,0,0,0,0,
1011,03:24:51,28,F,LAUNCH_PAD,1.0,40.7,92.4,3.4,1.3,0,0,0,0,0,0,17:29:47,820.2,38.3756,-79.6075,12,CXON,-0.0,0.0,-0.0,0.0,0.0,0.
1011,03:24:52,29,F,LAUNCH_PAD,1.1,40.7,92.4,3.5,1.1,0,0,0,0,0,0,
1011,03:24:53,30,F,LAUNCH_PAD,1.1,40.7,92.4,3.5,1.1,0,0,0,0,0,0,17:29:49,820.5,38.3756,-79.6075,12,CXON,-0.0,0.0,-0.0,0.0,0.0,0.
1011,03:24:54,31,F,LAUNCH_PAD,1.0,40.7,92.4,3.4,1.4,0,0,0,0,0,0,
1011,03:24:55,32,F,LAUNCH_PAD,1.1,40.7,92.4,3.5,1.1,0,0,0,0,0,0,17:29:51,820.5,38.3756,-79.6075,12,CXON,-0.0,0.0,-0.0,0.0,0.0,0.
1011,03:24:56,33,F,LAUNCH_PAD,1.1,40.7,92.4,3.5,1.0,0,0,0,0,0,0,
1011,03:24:57,34,F,LAUNCH_PAD,1.2,40.7,92.4,3.5,0.9,0,0,0,0,0,0,,-0.0,0.0,-0.0,0.0,0.0,0.0,-0.0,0.0,-0.0
1011,03:24:58,35,F,LAUNCH_PAD,1.2,40.7,92.4,3.4,1.1,0,0,0,0,0,0,17:29:54,820.7,38.3756,
1011,03:24:59,36,F,LAUNCH_PAD,1.2,40.7,92.4,3.5,1.1,0,0,0,0,0,0,
1011,03:25:00,37,F,LAUNCH_PAD,1.1,40.7,92.4,3.4,1.3,0,0,0,0,0,0,17:29:56,820.9,38.3756,-79.6075,12,CXON,-0.0,0.0,-0.0,0.0,0.0,0.
1011,03:25:01,38,F,LAUNCH_PAD,1.1,40.7,92.4,3.5,1.1,0,0,0,0,0,0,
1011,03:25:02,39,F,LAUNCH_PAD,1.1,40.7,92.4,3.4,1.4,0,0,0,0,0,0,17:29:58,821.0,38.3756,-79.6075,12,CXON,-0.0,0.0,-0.0,0.0,0.0,0.
1011,03:25:03,40,F,LAUNCH_PAD,1.2,40.7,92.4,3.4,1.4,0,0,0,0,0,0,
1011,03:25:04,41,F,LAUNCH_PAD,1.1,40.7,92.4,3.5,1.2,0,0,0,0,0,0,17:30:00,821.3,38.3756,-79.6075,12,CXON,-0.0,0.0,-0.0,0.0,0.0,0.
1011,03:25:05,42,F,LAUNCH_PAD,1.1,40.7,92.4,3.5,1.1,0,0,0,0,0,0,
1011,03:25:06,43,F,LAUNCH_PAD,1.2,40.7,92.4,3.4,1.3,0,0,0,0,0,0,17:30:02,821.6,38.3756,-79.6075,12,CXON,-0.0,0.0,-0.0,0.0,0.0,0.
1011,03:25:07,44,F,LAUNCH_PAD,1.1,40.7,92.4,3.4,1.3,0,0,0,0,0,0,
1011,03:25:08,45,F,LAUNCH_PAD,1.2,40.7,92.4,3.5,1.1,0,0,0,0,0,0,75,12,CXON,-0.0,0.0,-0.0,0.0,0.0,0.0,-0.0,0.0,-0.0
1011,03:25:09,46,F,LAUNCH_PAD,1.1,40.7,92.4,3.4,1.4,0,0,0,0,0,0,17:30:05,822.
1011,03:25:10,47,F,LAUNCH_PAD,1.1,40.7,92.4,3.4,1.3,0,0,0,0,0,0,-0.0
1011,03:25:11,48,F,LAUNCH_PAD,1.2,40.7,92.4,3.4,1.3,0,0,0,0,0,0,17:30:06,822.2,38.3756,-79.6075,12,CXON,-0.0,0.0,-0.0,0.0,0
1011,03:25:12,49,F,LAUNCH_PAD,1.2,40.7,92.4,3.5,1.1,0,0,0,0,0,0,
1011,03:25:13,50,F,LAUNCH_PAD,1.1,40.7,92.4,3.4,1.3,0,0,0,0,0,0,17:30:08,822.1,38.3756,-79.6075,12,CXON,-0.0,0.0,-0.0,0.0,0.0,0.
1011,03:25:14,51,F,LAUNCH_PAD,1.1,40.7,92.4,3.5,1.2,0,0,0,0,0,0,
1011,03:25:15,52,F,LAUNCH_PAD,1.1,40.7,92.4,3.4,1.2,0,0,0,0,0,0,17:30:10,822.1,38.3756,-79.6075,12,CXON,-0.0,0.0,-0.0,0.0,0.0,0.
1011,03:25:16,53,F,LAUNCH_PAD,1.2,40.7,92.4,3.5,0.9,0,0,0,0,0,0,
1011,03:25:17,54,F,LAUNCH_PAD,1.1,40.7,92.4,3.4,1.3,0,0,0,0,0,0,17:30:12,822.2,38.3756,-79.6075,12,CXON,-0.0,0.0,-0.0,0.0,0.0,0.
1011,03:25:18,55,F,LAUNCH_PAD,1.1,40.7,92.4,3.5,1.2,0,0,0,0,0,0,
1011,03:25:19,56,F,LAUNCH_PAD,1.1,40.7,92.4,3.4,1.2,0,0,0,0,0,0,756,-79.6075,12,CXON,-0.0,0.0,-0.0,0.0,0.0,0.0,-0.0,0.0,-0.0
1011,03:25:20,57,F,LAUNCH_PAD,1.2,40.7,92.4,3.5,0.9,0,0,0,0,0,0,17:
1011,03:25:21,58,F,LAUNCH_PAD,1.2,40.7,92.4,3.5,0.9,0,0,0,0,0,0,-0.0,0.0,-0.0
1011,03:25:22,59,F,LAUNCH_PAD,1.1,40.7,92.4,3.5,0.9,0,0,0,0,0,0,17:30:17,823.0,38.3756,-79.6075,12,CXON,-0.0,0.0,-
1011,03:25:23,60,F,LAUNCH_PAD,1.1,40.7,92.4,3.5,0.8,0,0,0,0,0,0,
1011,03:25:24,61,F,LAUNCH_PAD,1.1,40.7,92.4,3.5,1.0,0,0,0,0,0,0,17:30:19,823.4,38.3756,-79.6075,12,CXON,-0.0,0.0,-0.0,0.0,0.0,0.
1011,03:25:25,62,F,LAUNCH_PAD,1.1,40.7,92.4,3.5,1.1,0,0,0,0,0,0,
1011,03:25:26,63,F,LAUNCH_PAD,1.2,40.7,92.4,3.5,1.1,0,0,0,0,0,0,17:30:21,823.6,38.3756,-79.6075,12,CXON,-0.0,0.0,-0.0,0.0,0.0,0.
1011,03:25:27,64,F,LAUNCH_PAD,1.1,40.7,92.4,3.5,1.1,0,0,0,0,0,0,
1011,03:25:28,65,F,LAUNCH_PAD,1.1,40.7,92.4,3.4,1.4,0,0,0,0,0,0,17:30:23,823.7,38.3756,-79.6075,12,CXON,-0.0,0.0,-0.0,0.0,0.0,0.
1011,03:25:29,66,F,LAUNCH_PAD,1.1,40.7,92.4,3.4,1.4,0,0,0,0,0,0,
1011,03:25:30,67,F,LAUNCH_PAD,1.2,40.7,92.4,3.4,1.1,0,0,0,0,0,0,5,823.7,38.3756,-79.6075,12,CXON,-0.0,0.0,-0.0,0.0,0.0,0.0,-0.0,
1011,03:25:31,68,F,LAUNCH_PAD,1.1,40.7,92.4,3.5,1.1,0,0,0,0,0,0,
1011,03:25:32,69,F,LAUNCH_PAD,1.1,40.7,92.4,3.5,1.1,0,0,0,0,0,0,0.0,0.0,0.0,-0.0,0.0,-0.0
1011,03:25:33,70,F,LAUNCH_PAD,1.2,40.7,92.4,3.5,1.1,0,0,0,0,0,0,17:30:28,824.0,38.3756,-79.6075,12,CXO
1011,03:25:34,71,F,LAUNCH_PAD,1.3,40.7,92.4,3.4,1.1,0,0,0,0,0,0,
1011,03:25:35,72,F,LAUNCH_PAD,1.3,40.7,92.4,3.5,1.1,0,0,0,0,0,0,17:30:30,824.5,38.3756,-79.6075,12,CXON,-0.0,0.0,-0.0,0.0,0.0,0.
1011,03:25:36,73,F,LAUNCH_PAD,1.3,40.7,92.4,3.4,1.1,0,0,0,0,0,0,
1011,03:25:37,74,F,LAUNCH_PAD,1.2,40.7,92.4,3.4,1.2,0,0,0,0,0,0,17:30:32,824.8,38.3756,-79.6075,12,CXON,-0.0,0.0,-0.0,0.0,0.0,0.
1011,03:25:38,75,F,LAUNCH_PAD,1.3,40.7,92.4,3.5,1.1,0,0,0,0,0,0,
1011,03:25:39,76,F,LAUNCH_PAD,1.2,40.7,92.4,3.5,1.1,0,0,0,0,0,0,17:30:34,825.0,38.3756,-79.6075,12,CXON,-0.0,0.0,-0.0,0.0,0.0,0.
1011,03:25:40,77,F,LAUNCH_PAD,1.2,40.7,92.4,3.4,1.2,0,0,0,0,0,0,
1011,03:25:41,78,F,LAUNCH_PAD,1.2,40.7,92.4,3.4,1.1,0,0,0,0,0,0,:30:36,825.1,38.3756,-79.6075,12,CXON,-0.0,0.0,-0.0,0.0,0.0,0.0,
1011,03:25:42,79,F,LAUNCH_PAD,1.3,40.7,92.4,3.4,1.1,0,0,0,0,0,0,
1011,03:25:43,80,F,LAUNCH_PAD,1.2,40.7,92.4,3.5,1.0,0,0,0,0,0,0,-0.0,0.0,0.0,0.0,-0.0,0.0,-0.0
1011,03:25:44,81,F,LAUNCH_PAD,1.3,40.7,92.4,3.5,0.9,0,0,0,0,0,0,17:30:39,825.2,38.3756,-79.6075,1
1011,03:25:45,82,F,LAUNCH_PAD,1.3,40.7,92.4,3.5,0.9,0,0,0,0,0,0,
1011,03:25:46,83,F,LAUNCH_PAD,1.3,40.7,92.4,3.5,0.9,0,0,0,0,0,0,17:30:41,825.1,38.3756,-79.6075,12,CXON,-0.0,0.0,-0.0,0.0,0.0,0.
1011,03:25:47,84,F,LAUNCH_PAD,1.4,40.7,92.4,3.5,0.9,0,0,0,0,0,0,
1011,03:25:48,85,F,LAUNCH_PAD,1.4,40.7,92.4,3.5,0.9,0,0,0,0,0,0,17:30:43,825.2,38.3756,-79.6075,12,CXON,-0.0,0.0,-0.0,0.0,0.0,0.
1011,03:25:49,86,F,LAUNCH_PAD,1.4,40.7,92.4,3.5,1.1,0,0,0,0,0,0,
1011,03:25:50,87,F,LAUNCH_PAD,1.4,40.7,92.4,3.5,1.1,0,0,0,0,0,0,17:30:45,825.1,38.3756,-79.6075,12,CXON,-0.0,0.0,-0.0,0.0,0.0,0.
1011,03:25:51,88,F,LAUNCH_PAD,1.4,40.7,92.4,3.5,0.9,0,0,0,0,0,0,
1011,03:25:52,89,F,LAUNCH_PAD,1.4,40.7,92.4,3.5,0.9,0,0,0,0,0,0,17:30:47,824.9,38.3756,-79.6075,12,CXON,-0.0,0.0,-0.0,0.0,0.0,0.
1011,03:25:53,90,F,LAUNCH_PAD,1.5,40.7,92.4,3.5,0.9,0,0,0,0,0,0,
1011,03:25:54,91,F,LAUNCH_PAD,1.4,40.7,92.4,3.5,0.9,0,0,0,0,0,0,,0.0,-0.0,0.0,0.0,0.0,-0.0,0.0,-0.0
1011,03:25:55,92,F,LAUNCH_PAD,1.5,40.7,92.4,3.5,1.0,0,0,0,0,0,0,17:30:50,824.7,38.3756,-79.6
1011,03:25:56,93,F,LAUNCH_PAD,1.5,40.7,92.4,3.5,1.1,0,0,0,0,0,0,
1011,03:25:57,94,F,LAUNCH_PAD,1.4,40.7,92.4,3.4,1.1,0,0,0,0,0,0,17:30:52,824.3,38.3756,-79.6075,12,CXON,-0.0,0.0,-0.0,0.0,0.0,0.
1011,03:25:58,95,F,LAUNCH_PAD,1.4,40.7,92.4,3.5,1.0,0,0,0,0,0,0,
1011,03:25:59,96,F,LAUNCH_PAD,1.4,40.7,92.4,3.5,1.1,0,0,0,0,0,0,17:30:54,824.0,38.3756,-79.6075,12,CXON,-0.0,0.0,-0.0,0.0,0.0,0.
1011,03:26:00,97,F,LAUNCH_PAD,1.3,40.8,92.4,3.5,1.1,0,0,0,0,0,0,
1011,03:26:01,98,F,LAUNCH_PAD,1.4,40.7,92.4,3.5,1.1,0,0,0,0,0,0,17:30:56,823.6,38.3756,-79.6075,12,CXON,-0.0,0.0,-0.0,0.0,0.0,0.
1011,03:26:02,99,F,LAUNCH_PAD,1.3,40.7,92.4,3.5,1.1,0,0,0,0,0,0,
1011,03:26:03,100,F,LAUNCH_PAD,1.3,40.7,92.4,3.5,1.1,0,0,0,0,0,0,17:30:58,823.1,38.3756,-79.6075,12,CXON,-0.0,0.0,-0.0,0.0,0.0,0
1011,03:26:04,101,F,LAUNCH_PAD,1.3,40.8,92.4,3.5,1.1,0,0,0,0,0,0
1011,03:26:05,102,F,LAUNCH_PAD,1.3,40.8,92.4,3.5,1.1,0,0,0,0,0,079.6075,12,CXON,-0.0,0.0,-0.0,0.0,0.0,0.0,-0.0,0.0,-0.0
1011,03:26:06,103,F,LAUNCH_PAD,1.3,40.8,92.4,3.5,1.1,0,0,0,0,0,0,17:31:0
1011,03:26:07,104,F,LAUNCH_PAD,1.2,40.8,92.4,3.5,1.1,0,0,0,0,0,0.0,0.0,-0.0,0.0,-0.0
1011,03:26:08,105,F,LAUNCH_PAD,1.3,40.8,92.4,3.5,1.0,0,0,0,0,0,0,17:31:03,822.7,38.3756,-79.6075,12,CXON,-0
1011,03:26:09,106,F,LAUNCH_PAD,1.3,40.8,92.4,3.5,1.0,0,0,0,0,0,0
1011,03:26:10,107,F,LAUNCH_PAD,1.2,40.8,92.4,3.4,1.1,0,0,0,0,0,0,17:31:05,822.5,38.3756,-79.6075,12,CXON,-0.0,0.0,-0.0,0.0,0.0,0
1011,03:26:11,108,F,LAUNCH_PAD,1.2,40.8,92.4,3.5,1.2,0,0,0,0,0,0
1011,03:26:12,109,F,LAUNCH_PAD,1.3,40.8,92.4,3.4,1.1,0,0,0,0,0,0,17:31:07,821.3,38.3756,-79.6075,12,CXON,-0.0,0.0,-0.0,0.0,0.0,0
1011,03:26:13,110,F,LAUNCH_PAD,1.2,40.8,92.4,3.4,1.1,0,0,0,0,0,0
1011,03:26:14,111,F,LAUNCH_PAD,1.2,40.8,92.4,3.5,1.0,0,0,0,0,0,0,17:31:09,821.1,38.3756,-79.6075,12,CXON,-0.0,0.0,-0.0,0.0,0.0,0
1011,03:26:15,112,F,LAUNCH_PAD,1.2,40.8,92.4,3.5,0.9,0,0,0,0,0,0
1011,03:26:16,113,F,LAUNCH_PAD,1.2,40.8,92.4,3.5,0.9,0,0,0,0,0,0,17:31:11,820.6,38.3756,-79.6075,12,CXON,-0.0,0.0,-0.0,0.0,0.0,0
1011,03:26:17,114,F,LAUNCH_PAD,1.3,40.8,92.4,3.5,1.0,0,0,0,0,0,0
1011,03:26:18,115,F,LAUNCH_PAD,1.4,40.8,92.4,3.5,0.8,0,0,0,0,0,0,17:31:13,819.7,38.3756,-79.6075,12,CXON,-0.0,0.0,-0.0,0.0,0.0,0
1011,03:26:19,116,F,LAUNCH_PAD,1.3,40.8,92.4,3.5,0.8,0,0,0,0,0,0
1011,03:26:20,117,F,LAUNCH_PAD,1.4,40.8,92.4,3.5,1.0,0,0,0,0,0,06,-79.6075,12,CXON,-0.0,0.0,-0.0,0.0,0.0,0.0,-0.0,0.0,-0.0
1011,03:26:21,118,F,LAUNCH_PAD,1.4,40.8,92.4,3.5,0.9,0,0,0,0,0,0,17:3
1011,03:26:22,119,F,LAUNCH_PAD,1.3,40.8,92.4,3.5,0.9,0,0,0,0,0,0.0,0.0,0.0,-0.0,0.0,-0.0
1011,03:26:23,120,F,LAUNCH_PAD,1.4,40.8,92.4,3.5,0.9,0,0,0,0,0,0,17:31:18,818.8,38.3756,-79.6075,12,CXO
1011,03:26:24,121,F,LAUNCH_PAD,1.4,40.8,92.4,3.5,0.9,0,0,0,0,0,0
1011,03:26:25,122,F,LAUNCH_PAD,1.5,40.8,92.4,3.5,0.8,0,0,0,0,0,0,17:31:20,818.3,38.3756,-79.6075,12,CXON,-0.0,0.0,-0.0,0.0,0.0,0
1011,03:26:26,123,F,LAUNCH_PAD,1.3,40.8,92.4,3.5,0.9,0,0,0,0,0,0
1011,03:26:27,124,F,LAUNCH_PAD,1.4,40.8,92.4,3.5,1.1,0,0,0,0,0,0,17:31:22,818.4,38.3756,-79.6075,12,CXON,-0.0,0.0,-0.0,0.0,0.0,0
1011,03:26:28,125,F,LAUNCH_PAD,1.4,40.8,92.4,3.5,1.1,0,0,0,0,0,0
1011,03:26:29,126,F,LAUNCH_PAD,1.4,40.8,92.4,3.4,1.2,0,0,0,0,0,0,17:31:24,818.3,38.3756,-79.6075,12,CXON,-0.0,0.0,-0.0,0.0,0.0,0
1011,03:26:30,127,F,LAUNCH_PAD,1.4,40.8,92.4,3.4,1.1,0,0,0,0,0,0
1011,03:26:31,128,F,LAUNCH_PAD,1.3,40.8,92.4,3.5,1.1,0,0,0,0,0,0,17:31:26,818.0,38.3756,-79.6075,12,CXON,-0.0,0.0,-0.0,0.0,0.0,0
1011,03:26:32,129,F,LAUNCH_PAD,1.4,40.8,92.4,3.5,1.0,0,0,0,0,0,0
1011,03:26:33,130,F,LAUNCH_PAD,1.4,40.8,92.4,3.5,1.0,0,0,0,0,0,0,17:31:28,818.3,38.3756,-79.6075,12,CXON,-0.0,0.0,-0.0,0.0,0.0,0
1011,03:26:34,131,F,LAUNCH_PAD,1.4,40.8,92.4,3.5,1.1,0,0,0,0,0,0
1011,03:26:35,132,F,LAUNCH_PAD,1.4,40.8,92.4,3.5,1.1,0,0,0,0,0,0756,-79.6075,12,CXON,-0.0,0.0,-0.0,0.0,0.0,0.0,-0.0,0.0,-0.0
1011,03:26:36,133,F,LAUNCH_PAD,1.5,40.8,92.4,3.5,1.1,0,0,0,0,0,0,17
1011,03:26:37,134,F,LAUNCH_PAD,1.4,40.8,92.4,3.5,1.0,0,0,0,0,0,0.0,0.0,0.0,-0.0,0.0,-0.0
1011,03:26:38,135,F,LAUNCH_PAD,1.5,40.8,92.4,3.5,1.0,0,0,0,0,0,0,17:31:33,819.8,38.3756,-79.6075,12,CXO
1011,03:26:39,136,F,LAUNCH_PAD,1.4,40.8,92.4,3.5,1.1,0,0,0,0,0,0
1011,03:26:40,137,F,LAUNCH_PAD,1.6,40.8,92.4,3.5,1.1,0,0,0,0,0,0,17:31:35,820.4,38.3756,-79.6075,12,CXON,-0.0,0.0,-0.0,0.0,0.0,0
1011,03:26:41,138,F,LAUNCH_PAD,1.5,40.8,92.4,3.4,1.0,0,0,0,0,0,0
1011,03:26:42,139,F,LAUNCH_PAD,1.5,40.8,92.4,3.5,1.0,0,0,0,0,0,0,17:31:37,820.1,38.3756,-79.6075,12,CXON,-0.0,0.0,-0.0,0.0,0.0,0
1011,03:26:43,140,F,LAUNCH_PAD,1.4,40.8,92.4,3.5,1.1,0,0,0,0,0,0
1011,03:26:44,141,F,LAUNCH_PAD,1.4,40.8,92.4,3.5,1.0,0,0,0,0,0,0,17:31:39,819.3,38.3756,-79.6075,12,CXON,-0.0,0.0,-0.0,0.0,0.0,0
1011,03:26:45,142,F,LAUNCH_PAD,1.6,40.8,92.4,3.5,1.1,0,0,0,0,0,0
1011,03:26:46,143,F,LAUNCH_PAD,1.5,40.8,92.4,3.5,1.1,0,0,0,0,0,0,17:31:41,819.0,38.3756,-79.6075,12,CXON,-0.0,0.0,-0.0,0.0,0.0,0
1011,03:26:47,144,F,LAUNCH_PAD,1.5,40.8,92.4,3.5,1.1,0,0,0,0,0,0
1011,03:26:48,145,F,LAUNCH_PAD,1.6,40.8,92.4,3.4,1.2,0,0,0,0,0,0,17:31:43,818.9,38.3756,-79.6075,12,CXON,-0.0,0.0,-0.0,0.0,0.0,0
1011,03:26:49,146,F,LAUNCH_PAD,1.5,40.8,92.4,3.4,1.1,0,0,0,0,0,0
1011,03:26:50,147,F,LAUNCH_PAD,1.5,40.8,92.4,3.4,1.2,0,0,0,0,0,038.3756,-79.6075,12,CXON,-0.0,0.0,-0.0,0.0,0.0,0.0,-0.0,0.0,-0.0
1011,03:26:51,148,F,LAUNCH_PAD,1.5,40.8,92.4,3.4,1.2,0,0,0,0,0,0
1011,03:26:52,149,F,LAUNCH_PAD,1.6,40.8,92.4,3.4,1.1,0,0,0,0,0,0-0.0,0.0,0.0,0.0,-0.0,0.0,-0.0
1011,03:26:53,150,F,LAUNCH_PAD,1.5,40.8,92.4,3.5,1.1,0,0,0,0,0,0,17:31:48,817.9,38.3756,-79.6075,
1011,03:26:54,151,F,LAUNCH_PAD,1.4,40.8,92.4,3.5,0.9,0,0,0,0,0,0
1011,03:26:55,152,F,LAUNCH_PAD,1.4,40.8,92.4,3.5,0.9,0,0,0,0,0,0,17:31:50,817.8,38.3756,-79.6075,12,CXON,-0.0,0.0,-0.0,0.0,0.0,0
1011,03:26:56,153,F,LAUNCH_PAD,1.4,40.8,92.4,3.5,0.9,0,0,0,0,0,0
1011,03:26:57,154,F,LAUNCH_PAD,1.5,40.8,92.4,3.5,0.8,0,0,0,0,0,0,17:31:52,817.8,38.3756,-79.6075,12,CXON,-0.0,0.0,-0.0,0.0,0.0,0
1011,03:26:58,155,F,LAUNCH_PAD,1.3,40.8,92.4,3.5,0.9,0,0,0,0,0,0
1011,03:26:59,156,F,LAUNCH_PAD,1.3,40.8,92.4,3.5,0.9,0,0,0,0,0,0,17:31:54,817.6,38.3756,-79.6075,12,CXON,-0.0,0.0,-0.0,0.0,0.0,0
1011,03:27:00,157,F,LAUNCH_PAD,1.4,40.8,92.4,3.5,0.9,0,0,0,0,0,0
1011,03:27:01,158,F,LAUNCH_PAD,1.3,40.8,92.4,3.5,0.9,0,0,0,0,0,0,17:31:56,817.0,38.3756,-79.6075,12,CXON,-0.0,0.0,-0.0,0.0,0.0,0
1011,03:27:02,159,F,LAUNCH_PAD,1.3,40.8,92.4,3.5,0.9,0,0,0,0,0,0
1011,03:27:03,160,F,LAUNCH_PAD,1.4,40.8,92.4,3.5,0.9,0,0,0,0,0,0,17:31:58,817.0,38.3756,-79.6075,12,CXON,-0.0,0.0,-0.0,0.0,0.0,0
1011,03:27:04,161,F,LAUNCH_PAD,1.4,40.8,92.4,3.5,0.9,0,0,0,0,0,0
1011,03:27:05,162,F,LAUNCH_PAD,1.3,40.8,92.4,3.5,0.9,0,0,0,0,0,0,817.2,38.3756,-79.6075,12,CXON,-0.0,0.0,-0.0,0.0,0.0,0.0,-0.0,0
1011,03:27:06,163,F,LAUNCH_PAD,1.3,40.8,92.4,3.5,0.9,0,0,0,0,0,0
1011,03:27:07,164,F,LAUNCH_PAD,1.3,40.8,92.4,3.5,0.9,0,0,0,0,0,0,0.0,-0.0,0.0,0.0,0.0,-0.0,0.0,-0.0
1011,03:27:08,165,F,LAUNCH_PAD,1.3,40.8,92.4,3.5,1.0,0,0,0,0,0,0,17:32:03,817.3,38.3756,-79.
1011,03:27:09,166,F,LAUNCH_PAD,1.3,40.8,92.4,3.5,0.8,0,0,0,0,0,0
1011,03:27:10,167,F,LAUNCH_PAD,1.3,40.8,92.4,3.5,1.1,0,0,0,0,0,0,17:32:05,816.7,38.3756,-79.6075,12,CXON,-0.0,0.0,-0.0,0.0,0.0,0
1011,03:27:11,168,F,LAUNCH_PAD,1.3,40.8,92.4,3.5,1.1,0,0,0,0,0,0
1011,03:27:12,169,F,LAUNCH_PAD,1.2,40.8,92.4,3.5,1.1,0,0,0,0,0,0,17:32:07,816.4,38.3756,-79.6075,12,CXON,-0.0,0.0,-0.0,0.0,0.0,0
1011,03:27:13,170,F,LAUNCH_PAD,1.2,40.8,92.4,3.5,1.0,0,0,0,0,0,0
1011,03:27:14,171,F,LAUNCH_PAD,1.3,40.8,92.4,3.4,1.2,0,0,0,0,0,0,17:32:09,816.0,38.3756,-79.6075,12,CXON,-0.0,0.0,-0.0,0.0,0.0,0
1011,03:27:15,172,F,LAUNCH_PAD,1.2,40.8,92.4,3.5,1.0,0,0,0,0,0,0
1011,03:27:16,173,F,LAUNCH_PAD,1.3,40.8,92.4,3.5,1.0,0,0,0,0,0,0,17:32:11,815.5,38.3756,-79.6074,12,CXON,-0.0,0.0,-0.0,0.0,0.0,0
1011,03:27:17,174,F,LAUNCH_PAD,1.3,40.8,92.4,3.4,1.1,0,0,0,0,0,0
1011,03:27:18,175,F,LAUNCH_PAD,1.3,40.8,92.4,3.5,1.0,0,0,0,0,0,0,17:32:13,816.0,38.3756,-79.6074,12,CXON,-0.0,0.0,-0.0,0.0,0.0,0
1011,03:27:19,176,F,LAUNCH_PAD,1.3,40.8,92.4,3.5,1.0,0,0,0,0,0,0
1011,03:27:20,177,F,LAUNCH_PAD,1.4,40.8,92.4,3.4,1.2,0,0,0,0,0,015,815.8,38.3756,-79.6074,12,CXON,-0.0,0.0,-0.0,0.0,0.0,0.0,-0.0
1011,03:27:21,178,F,LAUNCH_PAD,1.4,40.8,92.4,3.5,1.0,0,0,0,0,0,0
1011,03:27:22,179,F,LAUNCH_PAD,1.3,40.8,92.4,3.5,1.1,0,0,0,0,0,0,-0.0,0.0,-0.0,0.0,0.0,0.0,-0.0,0.0,-0.0
1011,03:27:23,180,F,LAUNCH_PAD,1.3,40.8,92.4,3.4,1.1,0,0,0,0,0,0,17:32:18,815.7,38.3756
1011,03:27:24,181,F,LAUNCH_PAD,1.1,40.8,92.4,3.5,1.1,0,0,0,0,0,0-0.0
1011,03:27:25,182,F,LAUNCH_PAD,1.2,40.8,92.4,3.5,1.1,0,0,0,0,0,0,17:32:20,816.1,38.3756,-79.6074,12,CXON,-0.0,0.0,-0.0,0.0,
1011,03:27:26,183,F,LAUNCH_PAD,1.1,40.8,92.4,3.5,1.1,0,0,0,0,0,0
1011,03:27:27,184,F,LAUNCH_PAD,1.1,40.8,92.4,3.5,1.1,0,0,0,0,0,0,17:32:22,816.4,38.3756,-79.6074,12,CXON,-0.0,0.0,-0.0,0.0,0.0,0
1011,03:27:28,185,F,LAUNCH_PAD,1.1,40.8,92.4,3.5,1.1,0,0,0,0,0,0
1011,03:27:29,186,F,LAUNCH_PAD,1.2,40.8,92.4,3.5,1.1,0,0,0,0,0,0,17:32:24,817.0,38.3756,-79.6074,12,CXON,-0.0,0.0,-0.0,0.0,0.0,0
1011,03:27:30,187,F,LAUNCH_PAD,1.2,40.8,92.4,3.4,1.1,0,0,0,0,0,0
1011,03:27:31,188,F,LAUNCH_PAD,1.2,40.8,92.4,3.5,1.1,0,0,0,0,0,0,17:32:26,817.0,38.3756,-79.6074,12,CXON,-0.0,0.0,-0.0,0.0,0.0,0
1011,03:27:32,189,F,LAUNCH_PAD,1.2,40.8,92.4,3.5,1.1,0,0,0,0,0,0
1011,03:27:33,190,F,LAUNCH_PAD,1.1,40.8,92.4,3.4,1.1,0,0,0,0,0,0,17:32:28,816.9,38.3756,-79.6074,12,CXON,-0.0,0.0,-0.0,0.0,0.0,0
1011,03:27:34,191,F,LAUNCH_PAD,1.2,40.8,92.4,3.5,1.2,0,0,0,0,0,0
1011,03:27:35,192,F,LAUNCH_PAD,1.2,40.8,92.4,3.5,0.9,0,0,0,0,0,032:30,817.0,38.3756,-79.6074,12,CXON,-0.0,0.0,-0.0,0.0,0.0,0.0,-
1011,03:27:36,193,F,LAUNCH_PAD,1.2,40.8,92.4,3.5,0.9,0,0,0,0,0,0
1011,03:27:37,194,F,LAUNCH_PAD,1.3,40.9,92.4,3.5,0.9,0,0,0,0,0,0N,-0.0,0.0,-0.0,0.0,0.0,0.0,-0.0,0.0,-0.0
1011,03:27:38,195,F,LAUNCH_PAD,1.2,40.8,92.4,3.5,0.9,0,0,0,0,0,0,17:32:33,817.6,38.375
1011,03:27:39,196,F,LAUNCH_PAD,1.2,40.8,92.4,3.5,0.9,0,0,0,0,0,0,-0.0
1011,03:27:40,197,F,LAUNCH_PAD,1.3,40.8,92.4,3.5,0.8,0,0,0,0,0,0,17:32:35,818.3,38.3756,-79.6074,12,CXON,-0.0,0.0,-0.0,0.0
1011,03:27:41,198,F,LAUNCH_PAD,1.2,40.8,92.4,3.5,0.8,0,0,0,0,0,0
1011,03:27:42,199,F,LAUNCH_PAD,1.2,40.8,92.4,3.5,0.9,0,0,0,0,0,0,17:32:37,818.3,38.3756,-79.6074,12,CXON,-0.0,0.0,-0.0,0.0,0.0,0
1011,03:27:43,200,F,LAUNCH_PAD,1.2,40.9,92.4,3.5,0.9,0,0,0,0,0,0
1011,03:27:44,201,F,LAUNCH_PAD,1.1,40.8,92.4,3.5,0.9,0,0,0,0,0,0,17:32:39,818.4,38.3756,-79.6074,12,CXON,-0.0,0.0,-0.0,0.0,0.0,0
1011,03:27:45,202,F,LAUNCH_PAD,1.1,40.9,92.4,3.5,0.9,0,0,0,0,0,0
1011,03:27:46,203,F,LAUNCH_PAD,1.1,40.9,92.4,3.5,0.9,0,0,0,0,0,0,17:32:41,818.6,38.3756,-79.6074,12,CXON,-0.0,0.0,-0.0,0.0,0.0,0
1011,03:27:47,204,F,LAUNCH_PAD,1.1,40.9,92.4,3.5,0.9,0,0,0,0,0,0
1011,03:27:48,205,F,LAUNCH_PAD,1.1,40.8,92.4,3.5,0.9,0,0,0,0,0,0,17:32:43,818.8,38.3756,-79.6074,12,CXON,-0.0,0.0,-0.0,0.0,0.0,0
1011,03:27:49,206,F,LAUNCH_PAD,1.0,40.9,92.4,3.5,0.9,0,0,0,0,0,0
1011,03:27:50,207,F,LAUNCH_PAD,1.1,40.9,92.4,3.5,0.9,0,0,0,0,0,07:32:45,819.6,38.3756,-79.6074,12,CXON,-0.0,0.0,-0.0,0.0,0.0,0.0
1011,03:27:51,208,F,LAUNCH_PAD,1.1,40.9,92.4,3.5,0.8,0,0,0,0,0,0
1011,03:27:52,209,F,LAUNCH_PAD,1.1,40.8,92.4,3.5,1.1,0,0,0,0,0,0XON,-0.0,0.0,-0.0,0.0,0.0,0.0,-0.0,0.0,-0.0
1011,03:27:53,210,F,LAUNCH_PAD,1.1,40.8,92.4,3.5,1.0,0,0,0,0,0,0,17:32:48,819.6,38.3
1011,03:27:54,211,F,LAUNCH_PAD,1.1,40.9,92.4,3.5,1.1,0,0,0,0,0,0,0.0,-0.0
1011,03:27:55,212,F,LAUNCH_PAD,1.0,40.9,92.4,3.5,1.0,0,0,0,0,0,0,17:32:50,819.1,38.3756,-79.6074,12,CXON,-0.0,0.0,-0.0
1011,03:27:56,213,F,LAUNCH_PAD,1.0,40.9,92.4,3.5,1.1,0,0,0,0,0,0
1011,03:27:57,214,F,LAUNCH_PAD,1.1,40.9,92.4,3.5,1.0,0,0,0,0,0,0,17:32:52,818.7,38.3756,-79.6074,12,CXON,-0.0,0.0,-0.0,0.0,0.0,0
1011,03:27:58,215,F,LAUNCH_PAD,1.0,40.9,92.4,3.5,1.1,0,0,0,0,0,0
1011,03:27:59,216,F,LAUNCH_PAD,1.0,40.9,92.4,3.5,1.1,0,0,0,0,0,0,17:32:54,818.7,38.3756,-79.6075,12,CXON,-0.0,0.0,-0.0,0.0,0.0,0
1011,03:28:00,217,F,LAUNCH_PAD,0.9,40.9,92.4,3.5,1.0,0,0,0,0,0,0
1011,03:28:01,218,F,LAUNCH_PAD,1.0,40.9,92.4,3.5,1.1,0,0,0,0,0,0,17:32:56,818.5,38.3756,-79.6075,12,CXON,-0.0,0.0,-0.0,0.0,0.0,0
1011,03:28:02,219,F,LAUNCH_PAD,1.1,40.9,92.4,3.4,1.1,0,0,0,0,0,0
1011,03:28:03,220,F,LAUNCH_PAD,1.1,40.9,92.4,3.5,1.1,0,0,0,0,0,0,17:32:58,818.4,38.3756,-79.6075,12,CXON,-0.0,0.0,-0.0,0.0,0.0,0
1011,03:28:04,221,F,LAUNCH_PAD,1.0,40.9,92.4,3.4,1.1,0,0,0,0,0,0
1011,03:28:05,222,F,LAUNCH_PAD,1.0,40.9,92.4,3.5,1.2,0,0,0,0,0,0,17:33:00,818.0,38.3756,-79.6075,12,CXON,-0.0,0.0,-0.0,0.0,0.0,0
1011,03:28:06,223,F,LAUNCH_PAD,1.0,40.9,92.4,3.4,1.1,0,0,0,0,0,0
1011,03:28:07,224,F,LAUNCH_PAD,1.0,40.9,92.4,3.4,1.1,0,0,0,0,0,05,12,CXON,-0.0,0.0,-0.0,0.0,0.0,0.0,-0.0,0.0,-0.0
1011,03:28:08,225,F,LAUNCH_PAD,1.0,40.9,92.4,3.5,1.1,0,0,0,0,0,0,17:33:03,817.
1011,03:28:09,226,F,LAUNCH_PAD,1.0,40.9,92.4,3.4,1.1,0,0,0,0,0,0,-0.0,0.0,-0.0
1011,03:28:10,227,F,LAUNCH_PAD,1.0,40.9,92.4,3.4,1.1,0,0,0,0,0,0,17:33:05,817.3,38.3756,-79.6075,12,CXON,-0.0,0.0
1011,03:28:11,228,F,LAUNCH_PAD,0.9,40.9,92.4,3.5,1.1,0,0,0,0,0,0
1011,03:28:12,229,F,LAUNCH_PAD,1.0,40.9,92.4,3.5,0.9,0,0,0,0,0,0,17:33:07,817.2,38.3756,-79.6075,12,CXON,-0.0,0.0,-0.0,0.0,0.0,0
1011,03:28:13,230,F,LAUNCH_PAD,1.1,40.9,92.4,3.4,1.1,0,0,0,0,0,0
1011,03:28:14,231,F,LAUNCH_PAD,1.0,40.9,92.4,3.5,1.1,0,0,0,0,0,0,17:33:09,818.3,38.3756,-79.6075,12,CXON,-0.0,0.0,-0.0,0.0,0.0,0
1011,03:28:15,232,F,LAUNCH_PAD,1.0,40.9,92.4,3.5,0.9,0,0,0,0,0,0
1011,03:28:16,233,F,LAUNCH_PAD,0.9,40.9,92.4,3.5,0.9,0,0,0,0,0,0,17:33:11,818.9,38.3756,-79.6075,12,CXON,-0.0,0.0,-0.0,0.0,0.0,0
1011,03:28:17,234,F,LAUNCH_PAD,1.0,40.9,92.4,3.5,0.8,0,0,0,0,0,0
1011,03:28:18,235,F,LAUNCH_PAD,1.0,40.9,92.4,3.5,0.8,0,0,0,0,0,0,17:33:13,819.3,38.3756,-79.6075,12,CXON,-0.0,0.0,-0.0,0.0,0.0,0
1011,03:28:19,236,F,LAUNCH_PAD,1.0,40.9,92.4,3.4,1.1,0,0,0,0,0,0
1011,03:28:20,237,F,LAUNCH_PAD,1.0,40.9,92.4,3.5,0.9,0,0,0,0,0,0,17:33:15,819.5,38.3756,-79.6075,12,CXON,-0.0,0.0,-0.0,0.0,0.0,0
1011,03:28:21,238,F,LAUNCH_PAD,1.0,40.9,92.4,3.5,0.9,0,0,0,0,0,0
1011,03:28:22,239,F,LAUNCH_PAD,1.0,40.9,92.4,3.5,0.9,0,0,0,0,0,09.6075,12,CXON,-0.0,0.0,-0.0,0.0,0.0,0.0,-0.0,0.0,-0.0
1011,03:28:23,240,F,LAUNCH_PAD,1.0,40.9,92.4,3.5,0.9,0,0,0,0,0,0,17:33:18
1011,03:28:24,241,F,LAUNCH_PAD,1.0,40.9,92.4,3.4,1.1,0,0,0,0,0,00,0.0,-0.0,0.0,-0.0
1011,03:28:25,242,F,LAUNCH_PAD,1.0,40.9,92.4,3.5,1.1,0,0,0,0,0,0,17:33:20,819.9,38.3756,-79.6075,12,CXON,-0.
1011,03:28:26,243,F,LAUNCH_PAD,1.0,40.9,92.4,3.4,1.1,0,0,0,0,0,0
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

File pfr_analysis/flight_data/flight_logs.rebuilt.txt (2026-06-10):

1011,03:24:24,1,F,LAUNCH_PAD,0.8,40.6,92.4,3.4,1.3,0,0,0,0,0,0,17:29:20,820.6,38.3756,-79.6075,12,CXON,-0.0,0.0,-0.0,0.0,0.0,0.0,-0.0,0.0,-0.0
1011,03:24:25,2,F,LAUNCH_PAD,0.9,40.6,92.4,3.5,0.9,0,0,0,-2147483648,0,2147483647,17:29:21,820.7,38.3756,-79.6075,12,CXON,-0.0,0.0,-0.0,0.0,0.0,0.0,-0.0,0.0,-0.0
1011,03:24:26,3,F,LAUNCH_PAD,0.8,40.6,92.4,3.5,1.0,0,0,0,0,0,0,17:29:22,820.7,38.3756,-79.6075,12,CXON,-0.0,0.0,-0.0,0.0,0.0,0.0,-0.0,0.0,-0.0
1011,03:24:27,4,F,LAUNCH_PAD,0.7,40.6,92.4,3.5,1.1,0,0,0,0,0,0,17:29:23,820.7,38.3756,-79.6075,12,CXON,-0.0,0.0,-0.0,0.0,0.0,0.0,-0.0,0.0,-0.0
1011,03:24:28,5,F,LAUNCH_PAD,0.8,40.6,92.4,3.5,0.9,0,0,0,0,0,0,17:29:24,820.7,38.3756,-79.6075,12,CXON,-0.0,0.0,-0.0,0.0,0.0,0.0,-0.0,0.0,-0.0
1011,03:24:29,6,F,LAUNCH_PAD,0.8,40.6,92.4,3.4,1.3,0,0,0,0,0,0,17:29:25,820.6,38.3756,-79.6075,12,CXON,-0.0,0.0,-0.0,0.0,0.0,0.0,-0.0,0.0,-0.0
1011,03:24:30,7,F,LAUNCH_PAD,0.8,40.6,92.4,3.5,1.1,0,0,0,0,0,0,17:29:26,820.5,38.3756,-79.6075,12,CXON,-0.0,0.0,-0.0,0.0,0.0,0.0,-0.0,0.0,-0.0
1011,03:24:31,8,F,LAUNCH_PAD,0.8,40.6,92.4,3.4,1.1,0,0,0,0,0,0,17:29:27,820.3,38.3756,-79.6075,12,CXON,-0.0,0.0,-0.0,0.0,0.0,0.0,-0.0,0.0,-0.0
1011,03:24:32,9,F,LAUNCH_PAD,0.8,40.6,92.4,3.4,1.2,0,0,0,0,0,0,17:29:28,820.1,38.3756,-79.6075,12,CXON,-0.0,0.0,-0.0,0.0,0.0,0.0,-0.0,0.0,-0.0
1011,03:24:33,10,F,LAUNCH_PAD,0.8,40.6,92.4,3.4,1.2,0,0,0,0,0,0,17:29:29,819.9,38.3756,-79.6075,12,CXON,-0.0,0.0,-0.0,0.0,0.0,0.0,-0.0,0.0,-0.0
1011,03:24:34,11,F,LAUNCH_PAD,0.9,40.6,92.4,3.4,1.3,0,0,0,0,0,0,17:29:30,819.7,38.3756,-79.6075,12,CXON,-0.0,0.0,-0.0,0.0,0.0,0.0,-0.0,0.0,-0.0
1011,03:24:35,12,F,LAUNCH_PAD,0.8,40.6,92.4,3.4,1.3,0,0,0,0,0,0,17:29:31,819.6,38.3756,-79.6075,12,CXON,-0.0,0.0,-0.0,0.0,0.0,0.0,-0.0,0.0,-0.0
1011,03:24:36,13,F,LAUNCH_PAD,0.9,40.6,92.4,3.4,1.3,0,0,0,0,0,0,17:29:32,819.5,38.3756,-79.6075,12,CXON,-0.0,0.0,-0.0,0.0,0.0,0.0,-0.0,0.0,-0.0
1011,03:24:37,14,F,LAUNCH_PAD,0.9,40.6,92.4,3.4,1.2,0,0,0,0,0,0,17:29:33,819.4,38.3756,-79.6075,12,CXON,-0.0,0.0,-0.0,0.0,0.0,0.0,-0.0,0.0,-0.0
1011,03:24:38,15,F,LAUNCH_PAD,0.8,40.6,92.4,3.4,1.3,0,0,0,0,0,0,17:29:34,819.3,38.3756,-79.6075,12,CXON,-0.0,0.0,-0.0,0.0,0.0,0.0,-0.0,0.0,-0.0
1011,03:24:39,16,F,LAUNCH_PAD,0.9,40.6,92.4,3.4,1.2,0,0,0,0,0,0,17:29:35,819.2,38.3756,-79.6075,12,CXON,-0.0,0.0,-0.0,0.0,0.0,0.0,-0.0,0.0,-0.0
1011,03:24:40,17,F,LAUNCH_PAD,0.8,40.6,92.4,3.5,1.3,0,0,0,0,0,0,17:29:36,819.1,38.3756,-79.6075,12,CXON,-0.0,0.0,-0.0,0.0,0.0,0.0,-0.0,0.0,-0.0
1011,03:24:41,18,F,LAUNCH_PAD,0.8,40.6,92.4,3.4,1.3,0,0,0,0,0,0,17:29:37,819.1,38.3756,-79.6075,12,CXON,-0.0,0.0,-0.0,0.0,0.0,0.0,-0.0,0.0,-0.0
1011,03:24:42,19,F,LAUNCH_PAD,1.0,40.6,92.4,3.4,1.3,0,0,0,0,0,0,17:29:38,819.0,38.3756,-79.6075,12,CXON,-0.0,0.0,-0.0,0.0,0.0,0.0,-0.0,0.0,-0.0
1011,03:24:43,20,F,LAUNCH_PAD,1.0,40.7,92.4,3.4,1.4,0,0,0,0,0,0,17:29:
1011,03:24:44,21,F,LAUNCH_PAD,1.0,40.6,92.4,3.4,1.4,0,0,0,0,0,0,:40,819.0,38.3756,-79.6075,12,CXON,-0.0,0.0,-0.0,0.0,0.0,0.0,-0.
1011,03:24:45,22,F,LAUNCH_PAD,1.0,40.7,92.4,3.5,1.1,0,0,0,0,0,0,
1011,03:24:46,23,F,LAUNCH_PAD,1.0,40.6,92.4,3.4,1.4,0,0,0,0,0,0,0,0.0,0.0,0.0,-0.0,0.0,-0.0
1011,03:24:47,24,F,LAUNCH_PAD,1.1,40.7,92.4,3.5,1.0,0,0,0,0,0,0,17:29:43,819.3,38.3756,-79.6075,12,C
1011,03:24:48,25,F,LAUNCH_PAD,1.0,40.7,92.4,3.5,1.1,0,0,0,0,0,0,
1011,03:24:49,26,F,LAUNCH_PAD,1.0,40.7,92.4,3.4,1.4,0,0,0,0,0,0,17:29:45,819.8,38.3756,-79.6075,12,CXON,-0.0,0.0,-0.0,0.0,0.0,0.
1011,03:24:50,27,F,LAUNCH_PAD,1.0,40.7,92.4,3.5,1.1,0,0,0,0,0,0,
1011,03:24:51,28,F,LAUNCH_PAD,1.0,40.7,92.4,3.4,1.3,0,0,0,0,0,0,17:29:47,820.2,38.3756,-79.6075,12,CXON,-0.0,0.0,-0.0,0.0,0.0,0.
1011,03:24:52,29,F,LAUNCH_PAD,1.1,40.7,92.4,3.5,1.1,0,0,0,0,0,0,
1011,03:24:53,30,F,LAUNCH_PAD,1.1,40.7,92.4,3.5,1.1,0,0,0,0,0,0,17:29:49,820.5,38.3756,-79.6075,12,CXON,-0.0,0.0,-0.0,0.0,0.0,0.
1011,03:24:54,31,F,LAUNCH_PAD,1.0,40.7,92.4,3.4,1.4,0,0,0,0,0,0,
1011,03:24:55,32,F,LAUNCH_PAD,1.1,40.7,92.4,3.5,1.1,0,0,0,0,0,0,17:29:51,820.5,38.3756,-79.6075,12,CXON,-0.0,0.0,-0.0,0.0,0.0,0.
1011,03:24:56,33,F,LAUNCH_PAD,1.1,40.7,92.4,3.5,1.0,0,0,0,0,0,0,
1011,03:24:57,34,F,LAUNCH_PAD,1.2,40.7,92.4,3.5,0.9,0,0,0,0,0,0,,-0.0,0.0,-0.0,0.0,0.0,0.0,-0.0,0.0,-0.0
1011,03:24:58,35,F,LAUNCH_PAD,1.2,40.7,92.4,3.4,1.1,0,0,0,0,0,0,17:29:54,820.7,38.3756,
1011,03:24:59,36,F,LAUNCH_PAD,1.2,40.7,92.4,3.5,1.1,0,0,0,0,0,0,
1011,03:25:00,37,F,LAUNCH_PAD,1.1,40.7,92.4,3.4,1.3,0,0,0,0,0,0,17:29:56,820.9,38.3756,-79.6075,12,CXON,-0.0,0.0,-0.0,0.0,0.0,0.
1011,03:25:01,38,F,LAUNCH_PAD,1.1,40.7,92.4,3.5,1.1,0,0,0,0,0,0,
1011,03:25:02,39,F,LAUNCH_PAD,1.1,40.7,92.4,3.4,1.4,0,0,0,0,0,0,17:29:58,821.0,38.3756,-79.6075,12,CXON,-0.0,0.0,-0.0,0.0,0.0,0.
1011,03:25:03,40,F,LAUNCH_PAD,1.2,40.7,92.4,3.4,1.4,0,0,0,0,0,0,
1011,03:25:04,41,F,LAUNCH_PAD,1.1,40.7,92.4,3.5,1.2,0,0,0,0,0,0,17:30:00,821.3,38.3756,-79.6075,12,CXON,-0.0,0.0,-0.0,0.0,0.0,0.
1011,03:25:05,42,F,LAUNCH_PAD,1.1,40.7,92.4,3.5,1.1,0,0,0,0,0,0,
1011,03:25:06,43,F,LAUNCH_PAD,1.2,40.7,92.4,3.4,1.3,0,0,0,0,0,0,17:30:02,821.6,38.3756,-79.6075,12,CXON,-0.0,0.0,-0.0,0.0,0.0,0.
1011,03:25:07,44,F,LAUNCH_PAD,1.1,40.7,92.4,3.4,1.3,0,0,0,0,0,0,
1011,03:25:08,45,F,LAUNCH_PAD,1.2,40.7,92.4,3.5,1.1,0,0,0,0,0,0,75,12,CXON,-0.0,0.0,-0.0,0.0,0.0,0.0,-0.0,0.0,-0.0
1011,03:25:09,46,F,LAUNCH_PAD,1.1,40.7,92.4,3.4,1.4,0,0,0,0,0,0,17:30:05,822.
1011,03:25:10,47,F,LAUNCH_PAD,1.1,40.7,92.4,3.4,1.3,0,0,0,0,0,0,-0.0
1011,03:25:11,48,F,LAUNCH_PAD,1.2,40.7,92.4,3.4,1.3,0,0,0,0,0,0,17:30:06,822.2,38.3756,-79.6075,12,CXON,-0.0,0.0,-0.0,0.0,0
1011,03:25:12,49,F,LAUNCH_PAD,1.2,40.7,92.4,3.5,1.1,0,0,0,0,0,0,
1011,03:25:13,50,F,LAUNCH_PAD,1.1,40.7,92.4,3.4,1.3,0,0,0,0,0,0,17:30:08,822.1,38.3756,-79.6075,12,CXON,-0.0,0.0,-0.0,0.0,0.0,0.
1011,03:25:14,51,F,LAUNCH_PAD,1.1,40.7,92.4,3.5,1.2,0,0,0,0,0,0,
1011,03:25:15,52,F,LAUNCH_PAD,1.1,40.7,92.4,3.4,1.2,0,0,0,0,0,0,17:30:10,822.1,38.3756,-79.6075,12,CXON,-0.0,0.0,-0.0,0.0,0.0,0.
1011,03:25:16,53,F,LAUNCH_PAD,1.2,40.7,92.4,3.5,0.9,0,0,0,0,0,0,
1011,03:25:17,54,F,LAUNCH_PAD,1.1,40.7,92.4,3.4,1.3,0,0,0,0,0,0,17:30:12,822.2,38.3756,-79.6075,12,CXON,-0.0,0.0,-0.0,0.0,0.0,0.
1011,03:25:18,55,F,LAUNCH_PAD,1.1,40.7,92.4,3.5,1.2,0,0,0,0,0,0,
1011,03:25:19,56,F,LAUNCH_PAD,1.1,40.7,92.4,3.4,1.2,0,0,0,0,0,0,756,-79.6075,12,CXON,-0.0,0.0,-0.0,0.0,0.0,0.0,-0.0,0.0,-0.0
1011,03:25:20,57,F,LAUNCH_PAD,1.2,40.7,92.4,3.5,0.9,0,0,0,0,0,0,17:
1011,03:25:21,58,F,LAUNCH_PAD,1.2,40.7,92.4,3.5,0.9,0,0,0,0,0,0,-0.0,0.0,-0.0
1011,03:25:22,59,F,LAUNCH_PAD,1.1,40.7,92.4,3.5,0.9,0,0,0,0,0,0,17:30:17,823.0,38.3756,-79.6075,12,CXON,-0.0,0.0,-
1011,03:25:23,60,F,LAUNCH_PAD,1.1,40.7,92.4,3.5,0.8,0,0,0,0,0,0,
1011,03:25:24,61,F,LAUNCH_PAD,1.1,40.7,92.4,3.5,1.0,0,0,0,0,0,0,17:30:19,823.4,38.3756,-79.6075,12,CXON,-0.0,0.0,-0.0,0.0,0.0,0.
1011,03:25:25,62,F,LAUNCH_PAD,1.1,40.7,92.4,3.5,1.1,0,0,0,0,0,0,
1011,03:25:26,63,F,LAUNCH_PAD,1.2,40.7,92.4,3.5,1.1,0,0,0,0,0,0,17:30:21,823.6,38.3756,-79.6075,12,CXON,-0.0,0.0,-0.0,0.0,0.0,0.
1011,03:25:27,64,F,LAUNCH_PAD,1.1,40.7,92.4,3.5,1.1,0,0,0,0,0,0,
1011,03:25:28,65,F,LAUNCH_PAD,1.1,40.7,92.4,3.4,1.4,0,0,0,0,0,0,17:30:23,823.7,38.3756,-79.6075,12,CXON,-0.0,0.0,-0.0,0.0,0.0,0.
1011,03:25:29,66,F,LAUNCH_PAD,1.1,40.7,92.4,3.4,1.4,0,0,0,0,0,0,
1011,03:25:30,67,F,LAUNCH_PAD,1.2,40.7,92.4,3.4,1.1,0,0,0,0,0,0,5,823.7,38.3756,-79.6075,12,CXON,-0.0,0.0,-0.0,0.0,0.0,0.0,-0.0,
1011,03:25:31,68,F,LAUNCH_PAD,1.1,40.7,92.4,3.5,1.1,0,0,0,0,0,0,
1011,03:25:32,69,F,LAUNCH_PAD,1.1,40.7,92.4,3.5,1.1,0,0,0,0,0,0,0.0,0.0,0.0,-0.0,0.0,-0.0
1011,03:25:33,70,F,LAUNCH_PAD,1.2,40.7,92.4,3.5,1.1,0,0,0,0,0,0,17:30:28,824.0,38.3756,-79.6075,12,CXO
1011,03:25:34,71,F,LAUNCH_PAD,1.3,40.7,92.4,3.4,1.1,0,0,0,0,0,0,
1011,03:25:35,72,F,LAUNCH_PAD,1.3,40.7,92.4,3.5,1.1,0,0,0,0,0,0,17:30:30,824.5,38.3756,-79.6075,12,CXON,-0.0,0.0,-0.0,0.0,0.0,0.
1011,03:25:36,73,F,LAUNCH_PAD,1.3,40.7,92.4,3.4,1.1,0,0,0,0,0,0,
1011,03:25:37,74,F,LAUNCH_PAD,1.2,40.7,92.4,3.4,1.2,0,0,0,0,0,0,17:30:32,824.8,38.3756,-79.6075,12,CXON,-0.0,0.0,-0.0,0.0,0.0,0.
1011,03:25:38,75,F,LAUNCH_PAD,1.3,40.7,92.4,3.5,1.1,0,0,0,0,0,0,
1011,03:25:39,76,F,LAUNCH_PAD,1.2,40.7,92.4,3.5,1.1,0,0,0,0,0,0,17:30:34,825.0,38.3756,-79.6075,12,CXON,-0.0,0.0,-0.0,0.0,0.0,0.
1011,03:25:40,77,F,LAUNCH_PAD,1.2,40.7,92.4,3.4,1.2,0,0,0,0,0,0,
1011,03:25:41,78,F,LAUNCH_PAD,1.2,40.7,92.4,3.4,1.1,0,0,0,0,0,0,:30:36,825.1,38.3756,-79.6075,12,CXON,-0.0,0.0,-0.0,0.0,0.0,0.0,
1011,03:25:42,79,F,LAUNCH_PAD,1.3,40.7,92.4,3.4,1.1,0,0,0,0,0,0,
1011,03:25:43,80,F,LAUNCH_PAD,1.2,40.7,92.4,3.5,1.0,0,0,0,0,0,0,-0.0,0.0,0.0,0.0,-0.0,0.0,-0.0
1011,03:25:44,81,F,LAUNCH_PAD,1.3,40.7,92.4,3.5,0.9,0,0,0,0,0,0,17:30:39,825.2,38.3756,-79.6075,1
1011,03:25:45,82,F,LAUNCH_PAD,1.3,40.7,92.4,3.5,0.9,0,0,0,0,0,0,
1011,03:25:46,83,F,LAUNCH_PAD,1.3,40.7,92.4,3.5,0.9,0,0,0,0,0,0,17:30:41,825.1,38.3756,-79.6075,12,CXON,-0.0,0.0,-0.0,0.0,0.0,0.
1011,03:25:47,84,F,LAUNCH_PAD,1.4,40.7,92.4,3.5,0.9,0,0,0,0,0,0,
1011,03:25:48,85,F,LAUNCH_PAD,1.4,40.7,92.4,3.5,0.9,0,0,0,0,0,0,17:30:43,825.2,38.3756,-79.6075,12,CXON,-0.0,0.0,-0.0,0.0,0.0,0.
1011,03:25:49,86,F,LAUNCH_PAD,1.4,40.7,92.4,3.5,1.1,0,0,0,0,0,0,
1011,03:25:50,87,F,LAUNCH_PAD,1.4,40.7,92.4,3.5,1.1,0,0,0,0,0,0,17:30:45,825.1,38.3756,-79.6075,12,CXON,-0.0,0.0,-0.0,0.0,0.0,0.
1011,03:25:51,88,F,LAUNCH_PAD,1.4,40.7,92.4,3.5,0.9,0,0,0,0,0,0,
1011,03:25:52,89,F,LAUNCH_PAD,1.4,40.7,92.4,3.5,0.9,0,0,0,0,0,0,17:30:47,824.9,38.3756,-79.6075,12,CXON,-0.0,0.0,-0.0,0.0,0.0,0.
1011,03:25:53,90,F,LAUNCH_PAD,1.5,40.7,92.4,3.5,0.9,0,0,0,0,0,0,
1011,03:25:54,91,F,LAUNCH_PAD,1.4,40.7,92.4,3.5,0.9,0,0,0,0,0,0,,0.0,-0.0,0.0,0.0,0.0,-0.0,0.0,-0.0
1011,03:25:55,92,F,LAUNCH_PAD,1.5,40.7,92.4,3.5,1.0,0,0,0,0,0,0,17:30:50,824.7,38.3756,-79.6
1011,03:25:56,93,F,LAUNCH_PAD,1.5,40.7,92.4,3.5,1.1,0,0,0,0,0,0,
1011,03:25:57,94,F,LAUNCH_PAD,1.4,40.7,92.4,3.4,1.1,0,0,0,0,0,0,17:30:52,824.3,38.3756,-79.6075,12,CXON,-0.0,0.0,-0.0,0.0,0.0,0.
1011,03:25:58,95,F,LAUNCH_PAD,1.4,40.7,92.4,3.5,1.0,0,0,0,0,0,0,
1011,03:25:59,96,F,LAUNCH_PAD,1.4,40.7,92.4,3.5,1.1,0,0,0,0,0,0,17:30:54,824.0,38.3756,-79.6075,12,CXON,-0.0,0.0,-0.0,0.0,0.0,0.
1011,03:26:00,97,F,LAUNCH_PAD,1.3,40.8,92.4,3.5,1.1,0,0,0,0,0,0,
1011,03:26:01,98,F,LAUNCH_PAD,1.4,40.7,92.4,3.5,1.1,0,0,0,0,0,0,17:30:56,823.6,38.3756,-79.6075,12,CXON,-0.0,0.0,-0.0,0.0,0.0,0.
1011,03:26:02,99,F,LAUNCH_PAD,1.3,40.7,92.4,3.5,1.1,0,0,0,0,0,0,
1011,03:26:03,100,F,LAUNCH_PAD,1.3,40.7,92.4,3.5,1.1,0,0,0,0,0,0,17:30:58,823.1,38.3756,-79.6075,12,CXON,-0.0,0.0,-0.0,0.0,0.0,0
1011,03:26:04,101,F,LAUNCH_PAD,1.3,40.8,92.4,3.5,1.1,0,0,0,0,0,0
1011,03:26:05,102,F,LAUNCH_PAD,1.3,40.8,92.4,3.5,1.1,0,0,0,0,0,079.6075,12,CXON,-0.0,0.0,-0.0,0.0,0.0,0.0,-0.0,0.0,-0.0
1011,03:26:06,103,F,LAUNCH_PAD,1.3,40.8,92.4,3.5,1.1,0,0,0,0,0,0,17:31:0
1011,03:26:07,104,F,LAUNCH_PAD,1.2,40.8,92.4,3.5,1.1,0,0,0,0,0,0.0,0.0,-0.0,0.0,-0.0
1011,03:26:08,105,F,LAUNCH_PAD,1.3,40.8,92.4,3.5,1.0,0,0,0,0,0,0,17:31:03,822.7,38.3756,-79.6075,12,CXON,-0
1011,03:26:09,106,F,LAUNCH_PAD,1.3,40.8,92.4,3.5,1.0,0,0,0,0,0,0
1011,03:26:10,107,F,LAUNCH_PAD,1.2,40.8,92.4,3.4,1.1,0,0,0,0,0,0,17:31:05,822.5,38.3756,-79.6075,12,CXON,-0.0,0.0,-0.0,0.0,0.0,0
1011,03:26:11,108,F,LAUNCH_PAD,1.2,40.8,92.4,3.5,1.2,0,0,0,0,0,0
1011,03:26:12,109,F,LAUNCH_PAD,1.3,40.8,92.4,3.4,1.1,0,0,0,0,0,0,17:31:07,821.3,38.3756,-79.6075,12,CXON,-0.0,0.0,-0.0,0.0,0.0,0
1011,03:26:13,110,F,LAUNCH_PAD,1.2,40.8,92.4,3.4,1.1,0,0,0,0,0,0
1011,03:26:14,111,F,LAUNCH_PAD,1.2,40.8,92.4,3.5,1.0,0,0,0,0,0,0,17:31:09,821.1,38.3756,-79.6075,12,CXON,-0.0,0.0,-0.0,0.0,0.0,0
1011,03:26:15,112,F,LAUNCH_PAD,1.2,40.8,92.4,3.5,0.9,0,0,0,0,0,0
1011,03:26:16,113,F,LAUNCH_PAD,1.2,40.8,92.4,3.5,0.9,0,0,0,0,0,0,17:31:11,820.6,38.3756,-79.6075,12,CXON,-0.0,0.0,-0.0,0.0,0.0,0
1011,03:26:17,114,F,LAUNCH_PAD,1.3,40.8,92.4,3.5,1.0,0,0,0,0,0,0
1011,03:26:18,115,F,LAUNCH_PAD,1.4,40.8,92.4,3.5,0.8,0,0,0,0,0,0,17:31:13,819.7,38.3756,-79.6075,12,CXON,-0.0,0.0,-0.0,0.0,0.0,0
1011,03:26:19,116,F,LAUNCH_PAD,1.3,40.8,92.4,3.5,0.8,0,0,0,0,0,0
1011,03:26:20,117,F,LAUNCH_PAD,1.4,40.8,92.4,3.5,1.0,0,0,0,0,0,06,-79.6075,12,CXON,-0.0,0.0,-0.0,0.0,0.0,0.0,-0.0,0.0,-0.0
1011,03:26:21,118,F,LAUNCH_PAD,1.4,40.8,92.4,3.5,0.9,0,0,0,0,0,0,17:3
1011,03:26:22,119,F,LAUNCH_PAD,1.3,40.8,92.4,3.5,0.9,0,0,0,0,0,0.0,0.0,0.0,-0.0,0.0,-0.0
1011,03:26:23,120,F,LAUNCH_PAD,1.4,40.8,92.4,3.5,0.9,0,0,0,0,0,0,17:31:18,818.8,38.3756,-79.6075,12,CXO
1011,03:26:24,121,F,LAUNCH_PAD,1.4,40.8,92.4,3.5,0.9,0,0,0,0,0,0
1011,03:26:25,122,F,LAUNCH_PAD,1.5,40.8,92.4,3.5,0.8,0,0,0,0,0,0,17:31:20,818.3,38.3756,-79.6075,12,CXON,-0.0,0.0,-0.0,0.0,0.0,0
1011,03:26:26,123,F,LAUNCH_PAD,1.3,40.8,92.4,3.5,0.9,0,0,0,0,0,0
1011,03:26:27,124,F,LAUNCH_PAD,1.4,40.8,92.4,3.5,1.1,0,0,0,0,0,0,17:31:22,818.4,38.3756,-79.6075,12,CXON,-0.0,0.0,-0.0,0.0,0.0,0
1011,03:26:28,125,F,LAUNCH_PAD,1.4,40.8,92.4,3.5,1.1,0,0,0,0,0,0
1011,03:26:29,126,F,LAUNCH_PAD,1.4,40.8,92.4,3.4,1.2,0,0,0,0,0,0,17:31:24,818.3,38.3756,-79.6075,12,CXON,-0.0,0.0,-0.0,0.0,0.0,0
1011,03:26:30,127,F,LAUNCH_PAD,1.4,40.8,92.4,3.4,1.1,0,0,0,0,0,0
1011,03:26:31,128,F,LAUNCH_PAD,1.3,40.8,92.4,3.5,1.1,0,0,0,0,0,0,17:31:26,818.0,38.3756,-79.6075,12,CXON,-0.0,0.0,-0.0,0.0,0.0,0
1011,03:26:32,129,F,LAUNCH_PAD,1.4,40.8,92.4,3.5,1.0,0,0,0,0,0,0
1011,03:26:33,130,F,LAUNCH_PAD,1.4,40.8,92.4,3.5,1.0,0,0,0,0,0,0,17:31:28,818.3,38.3756,-79.6075,12,CXON,-0.0,0.0,-0.0,0.0,0.0,0
1011,03:26:34,131,F,LAUNCH_PAD,1.4,40.8,92.4,3.5,1.1,0,0,0,0,0,0
1011,03:26:35,132,F,LAUNCH_PAD,1.4,40.8,92.4,3.5,1.1,0,0,0,0,0,0756,-79.6075,12,CXON,-0.0,0.0,-0.0,0.0,0.0,0.0,-0.0,0.0,-0.0
1011,03:26:36,133,F,LAUNCH_PAD,1.5,40.8,92.4,3.5,1.1,0,0,0,0,0,0,17
1011,03:26:37,134,F,LAUNCH_PAD,1.4,40.8,92.4,3.5,1.0,0,0,0,0,0,0.0,0.0,0.0,-0.0,0.0,-0.0
1011,03:26:38,135,F,LAUNCH_PAD,1.5,40.8,92.4,3.5,1.0,0,0,0,0,0,0,17:31:33,819.8,38.3756,-79.6075,12,CXO
1011,03:26:39,136,F,LAUNCH_PAD,1.4,40.8,92.4,3.5,1.1,0,0,0,0,0,0
1011,03:26:40,137,F,LAUNCH_PAD,1.6,40.8,92.4,3.5,1.1,0,0,0,0,0,0,17:31:35,820.4,38.3756,-79.6075,12,CXON,-0.0,0.0,-0.0,0.0,0.0,0
1011,03:26:41,138,F,LAUNCH_PAD,1.5,40.8,92.4,3.4,1.0,0,0,0,0,0,0
1011,03:26:42,139,F,LAUNCH_PAD,1.5,40.8,92.4,3.5,1.0,0,0,0,0,0,0,17:31:37,820.1,38.3756,-79.6075,12,CXON,-0.0,0.0,-0.0,0.0,0.0,0
1011,03:26:43,140,F,LAUNCH_PAD,1.4,40.8,92.4,3.5,1.1,0,0,0,0,0,0
1011,03:26:44,141,F,LAUNCH_PAD,1.4,40.8,92.4,3.5,1.0,0,0,0,0,0,0,17:31:39,819.3,38.3756,-79.6075,12,CXON,-0.0,0.0,-0.0,0.0,0.0,0
1011,03:26:45,142,F,LAUNCH_PAD,1.6,40.8,92.4,3.5,1.1,0,0,0,0,0,0
1011,03:26:46,143,F,LAUNCH_PAD,1.5,40.8,92.4,3.5,1.1,0,0,0,0,0,0,17:31:41,819.0,38.3756,-79.6075,12,CXON,-0.0,0.0,-0.0,0.0,0.0,0
1011,03:26:47,144,F,LAUNCH_PAD,1.5,40.8,92.4,3.5,1.1,0,0,0,0,0,0
1011,03:26:48,145,F,LAUNCH_PAD,1.6,40.8,92.4,3.4,1.2,0,0,0,0,0,0,17:31:43,818.9,38.3756,-79.6075,12,CXON,-0.0,0.0,-0.0,0.0,0.0,0
1011,03:26:49,146,F,LAUNCH_PAD,1.5,40.8,92.4,3.4,1.1,0,0,0,0,0,0
1011,03:26:50,147,F,LAUNCH_PAD,1.5,40.8,92.4,3.4,1.2,0,0,0,0,0,038.3756,-79.6075,12,CXON,-0.0,0.0,-0.0,0.0,0.0,0.0,-0.0,0.0,-0.0
1011,03:26:51,148,F,LAUNCH_PAD,1.5,40.8,92.4,3.4,1.2,0,0,0,0,0,0
1011,03:26:52,149,F,LAUNCH_PAD,1.6,40.8,92.4,3.4,1.1,0,0,0,0,0,0-0.0,0.0,0.0,0.0,-0.0,0.0,-0.0
1011,03:26:53,150,F,LAUNCH_PAD,1.5,40.8,92.4,3.5,1.1,0,0,0,0,0,0,17:31:48,817.9,38.3756,-79.6075,
1011,03:26:54,151,F,LAUNCH_PAD,1.4,40.8,92.4,3.5,0.9,0,0,0,0,0,0
1011,03:26:55,152,F,LAUNCH_PAD,1.4,40.8,92.4,3.5,0.9,0,0,0,0,0,0,17:31:50,817.8,38.3756,-79.6075,12,CXON,-0.0,0.0,-0.0,0.0,0.0,0
1011,03:26:56,153,F,LAUNCH_PAD,1.4,40.8,92.4,3.5,0.9,0,0,0,0,0,0
1011,03:26:57,154,F,LAUNCH_PAD,1.5,40.8,92.4,3.5,0.8,0,0,0,0,0,0,17:31:52,817.8,38.3756,-79.6075,12,CXON,-0.0,0.0,-0.0,0.0,0.0,0
1011,03:26:58,155,F,LAUNCH_PAD,1.3,40.8,92.4,3.5,0.9,0,0,0,0,0,0
1011,03:26:59,156,F,LAUNCH_PAD,1.3,40.8,92.4,3.5,0.9,0,0,0,0,0,0,17:31:54,817.6,38.3756,-79.6075,12,CXON,-0.0,0.0,-0.0,0.0,0.0,0
1011,03:27:00,157,F,LAUNCH_PAD,1.4,40.8,92.4,3.5,0.9,0,0,0,0,0,0
1011,03:27:01,158,F,LAUNCH_PAD,1.3,40.8,92.4,3.5,0.9,0,0,0,0,0,0,17:31:56,817.0,38.3756,-79.6075,12,CXON,-0.0,0.0,-0.0,0.0,0.0,0
1011,03:27:02,159,F,LAUNCH_PAD,1.3,40.8,92.4,3.5,0.9,0,0,0,0,0,0
1011,03:27:03,160,F,LAUNCH_PAD,1.4,40.8,92.4,3.5,0.9,0,0,0,0,0,0,17:31:58,817.0,38.3756,-79.6075,12,CXON,-0.0,0.0,-0.0,0.0,0.0,0
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

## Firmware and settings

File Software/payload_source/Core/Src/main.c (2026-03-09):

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
/* Includes ------------------------------------------------------------------*/
#include "main.h"

/* USER CODE BEGIN Includes */
#ifdef __cplusplus
 extern "C" {
#endif
void main_cpp();
#ifdef __cplusplus
}
#endif
/* USER CODE END Includes */


COM_InitTypeDef BspCOMInit;

I2C_HandleTypeDef hi2c1;

SPI_HandleTypeDef hspi1;

TIM_HandleTypeDef htim1;
TIM_HandleTypeDef htim2;
TIM_HandleTypeDef htim3;
TIM_HandleTypeDef htim4;

UART_HandleTypeDef huart1;

/* USER CODE BEGIN PV */
volatile uint8_t send_flag = 0;
volatile uint8_t pvd_flag = 0;
uint8_t rx_byte;
volatile char rx_buff[128];
volatile uint8_t rx_idx = 0;
volatile uint8_t cmd_ready = 0;
volatile uint8_t discard_flag = 0;
/* USER CODE END PV */

void SystemClock_Config(void);
static void MX_GPIO_Init(void);
static void MX_I2C1_Init(void);
static void MX_SPI1_Init(void);
static void MX_TIM1_Init(void);
static void MX_USART1_UART_Init(void);
static void MX_TIM2_Init(void);
static void MX_TIM3_Init(void);
static void MX_TIM4_Init(void);
/**
  * @brief  The application entry point.
  * @retval int
  */
int main(void)
{

  /* MCU Configuration--------------------------------------------------------*/

  /* Reset of all peripherals, Initializes the Flash interface and the Systick. */
  HAL_Init();

  /* Configure the system clock */
  SystemClock_Config();

  /* Initialize all configured peripherals */
  MX_GPIO_Init();
  MX_I2C1_Init();
  MX_SPI1_Init();
  MX_TIM1_Init();
  MX_USART1_UART_Init();
  MX_TIM2_Init();
  MX_TIM3_Init();
  MX_TIM4_Init();
  /* USER CODE BEGIN 2 */

  HAL_UART_Receive_IT(&huart1, &rx_byte, 1);

  /* USER CODE END 2 */

  /* Initialize leds */
  BSP_LED_Init(LED_GREEN);

  /* Initialize COM1 port (115200, 8 bits (7-bit data + 1 stop bit), no parity */
  BspCOMInit.BaudRate   = 115200;
  BspCOMInit.WordLength = COM_WORDLENGTH_8B;
  BspCOMInit.StopBits   = COM_STOPBITS_1;
  BspCOMInit.Parity     = COM_PARITY_NONE;
  BspCOMInit.HwFlowCtl  = COM_HWCONTROL_NONE;
  if (BSP_COM_Init(COM1, &BspCOMInit) != BSP_ERROR_NONE)
  {
    Error_Handler();
  }

  /* Infinite loop */
  /* USER CODE BEGIN WHILE */
  main_cpp();
  while (1)
  {

    /* USER CODE END WHILE */

    /* USER CODE BEGIN 3 */
  }
  /* USER CODE END 3 */
}

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
/* USER CODE BEGIN 4 */
void HAL_TIM_PeriodElapsedCallback(TIM_HandleTypeDef* htim)
{
  if(htim == &htim1) 
  {
    send_flag = 1;
  }
}

void HAL_PWR_PVDCallback(void)
{
  pvd_flag = 1;
}

void HAL_UART_RxCpltCallback(UART_HandleTypeDef* huart)
{
	if(huart->Instance == USART1)
	{
		if(!cmd_ready)
		{
			if(discard_flag)
			{
				if(rx_byte == '\r' || rx_idx == sizeof(rx_buff))
				{
					discard_flag = 0;
				}
			}
			else
			{
				if(rx_byte == '\r')
				{
					rx_buff[rx_idx] = '\0';
					cmd_ready = 1;
					rx_idx = 0;
				}
				else
				{
					rx_buff[rx_idx++] = rx_byte;
					if(rx_idx > sizeof(rx_buff))
					{
						rx_idx = 0;
					}
				}
			}
		}
		else
		{
			discard_flag = 1;
		}

		HAL_UART_Receive_IT(&huart1, &rx_byte, 1);
	}
}
/* USER CODE END 4 */

/* USER CODE BEGIN Header */
/**
  ******************************************************************************
  * @file           : main.c
  * @brief          : Main program body
  ******************************************************************************
  * @attention
  *
  * Copyright (c) 2025 STMicroelectronics.
  * All rights reserved.
  *
  * This software is licensed under terms that can be found in the LICENSE file
  * in the root directory of this software component.
  * If no LICENSE file comes with this software, it is provided AS-IS.
  *
  ******************************************************************************
  */
/* USER CODE END Header */

/**
  * @}
  */

/**
  * @}
  */

/**
  * @brief  This function is executed in case of error occurrence.
  * @retval None
  */
void Error_Handler(void)
{
  /* USER CODE BEGIN Error_Handler_Debug */
  /* User can add his own implementation to report the HAL error return state */
  __disable_irq();
  while (1)
  {
  }
  /* USER CODE END Error_Handler_Debug */
}
#ifdef USE_FULL_ASSERT
/**
  * @brief  Reports the name of the source file and the source line number
  *         where the assert_param error has occurred.
  * @param  file: pointer to the source file name
  * @param  line: assert_param error line source number
  * @retval None
  */
void assert_failed(uint8_t *file, uint32_t line)
{
  /* USER CODE BEGIN 6 */
  /* User can add his own implementation to report the file name and line number,
     ex: printf("Wrong parameters value: file %s on line %d\r\n", file, line) */
  /* USER CODE END 6 */
}
#endif /* USE_FULL_ASSERT */

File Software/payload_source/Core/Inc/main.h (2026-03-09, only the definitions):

#define G_CAM_OUT_Pin GPIO_PIN_0
#define G_CAM_OUT_GPIO_Port GPIOF
#define PG_CAM_OUT_Pin GPIO_PIN_1
#define PG_CAM_OUT_GPIO_Port GPIOF
#define SERVO_WING_DIR_Pin GPIO_PIN_0
#define SERVO_WING_DIR_GPIO_Port GPIOA
#define SERVO_WING_PWM_Pin GPIO_PIN_1
#define SERVO_WING_PWM_GPIO_Port GPIOA
#define SPI_CS_GPIO_OUT_Pin GPIO_PIN_4
#define SPI_CS_GPIO_OUT_GPIO_Port GPIOA
#define SERVO_EGG_REL_Pin GPIO_PIN_0
#define SERVO_EGG_REL_GPIO_Port GPIOB
#define PG_CAM_IN_Pin GPIO_PIN_8
#define PG_CAM_IN_GPIO_Port GPIOA
#define XBEE_TX_Pin GPIO_PIN_9
#define XBEE_TX_GPIO_Port GPIOA
#define XBEE_RX_Pin GPIO_PIN_10
#define XBEE_RX_GPIO_Port GPIOA
#define SERVO_CC_REL_Pin GPIO_PIN_11
#define SERVO_CC_REL_GPIO_Port GPIOA
#define SERVO_NC_REL_Pin GPIO_PIN_12
#define SERVO_NC_REL_GPIO_Port GPIOA
#define T_SWDIO_Pin GPIO_PIN_13
#define T_SWDIO_GPIO_Port GPIOA
#define T_SWCLK_Pin GPIO_PIN_14
#define T_SWCLK_GPIO_Port GPIOA
#define I2C_SCL_Pin GPIO_PIN_15
#define I2C_SCL_GPIO_Port GPIOA
#define T_SWO_Pin GPIO_PIN_3
#define T_SWO_GPIO_Port GPIOB
#define SERVO_ELEVATOR_Pin GPIO_PIN_4
#define SERVO_ELEVATOR_GPIO_Port GPIOB
#define SERVO_AILERON_Pin GPIO_PIN_5
#define SERVO_AILERON_GPIO_Port GPIOB
#define G_CAM_IN_Pin GPIO_PIN_6
#define G_CAM_IN_GPIO_Port GPIOB
#define I2C_SDA_Pin GPIO_PIN_7
#define I2C_SDA_GPIO_Port GPIOB

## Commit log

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2025-10-04 Organizing KiCad models
    [CanSat_Power_Management_Board.kicad_pcb, CanSat_Power_Management_Board.kicad_sch, Onboarding_Example.kicad_pcb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]
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2025-10-07 Moving time of flight sensor code into the correct area
    [vl53l1-satel.ino]
2025-10-07 Temp removal of software files
    [cansat_data.csv]
2025-10-07 Adding back folder
    [cansat_data.csv]
2025-10-07 Reorganizing electrical folder
    [CanSat_Power_Management_Board.kicad_pcb, CanSat_Power_Management_Board.kicad_sch, Onboarding_Example.kicad_pcb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]
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2025-10-11 Temp buzzer pin config file
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2025-10-18 Adding pin config for buzzer
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2025-11-01 Add schematic for buzzer
    [Buzzer.kicad_pcb, Buzzer.kicad_sch]
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2025-11-23 ubuntu venv for gnd station
    [pyvenv.cfg]
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2026-01-18 Initial board setting commit
    [capybara_rocket.kicad_pcb, capybara_rocket.kicad_sch]
2026-01-25 Adding new KiCad symbols and footprints and initial PCB dimension work
    [capybara_rocket.kicad_pcb, capybara_rocket.kicad_sch]
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2026-02-07 pcb board update w/ new symbols, footprints, and 3dmodels
    [capybara_rocket.kicad_pcb, capybara_rocket.kicad_sch]
2026-02-08 Adding buck boost components
    [capybara_rocket.kicad_pcb, capybara_rocket.kicad_sch]
2026-02-08 orgnaization raspi trackpad transpose remove duplicate file
    [telemetry_data.csv]
2026-02-08 PCB board arrangement update and Adafruit INA219 full footprint design
    [capybara_rocket.kicad_pcb]
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2026-02-12 Initial commit for Ground Station board and rest of the active components
    [capybara_habitat.kicad_pcb, capybara_habitat.kicad_sch]
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2026-02-13 Revert "Updating ignored KiCad files"
    This reverts commit 65e8428f164b31f1042735344671e9e3e88eaf99.
2026-02-13 Revert "Revert "Updating ignored KiCad files""
    This reverts commit a34014a7b1bb2db558114653bc938ac35c5088f0.
2026-02-13 Fixing KiCad issues
2026-02-13 Resolved symbol/footprint issue
    [capybara_habitat.kicad_pcb, capybara_habitat.kicad_sch]
2026-02-16 Adding GNSS 3D model
    [capybara_rocket.kicad_pcb]
2026-02-16 Updating GPS footprint and CPL board
    [capybara_rocket.kicad_pcb]
2026-02-17 Major CPL PCB work update
    [capybara_rocket.kicad_pcb, capybara_rocket.kicad_sch]
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2026-02-22 some work on datasheets
    [main.kicad_pcb, main.kicad_sch]
2026-03-08 March 8th updates
    [capybara_rocket.kicad_sch]
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2026-03-10 Adding BMP581 KiCad models and big boi updates to CPL PCB
    [capybara_habitat.kicad_pcb, capybara_habitat.kicad_sch, capybara_rocket.kicad_pcb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]
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2026-03-11 Removing duplicated ground station board
    [main.kicad_pcb, main.kicad_sch]
2026-03-15 March 15 CPL PCB update
    [capybara_rocket.kicad_pcb, capybara_rocket.kicad_sch]
2026-03-15 Fixing gitignore of backup KiCad .zip files
2026-03-15 LT3536 and MP3414 circuit design
    [capybara_rocket.kicad_pcb, capybara_rocket.kicad_sch]
2026-03-15 MAX756 circuit design
    [capybara_rocket.kicad_pcb, capybara_rocket.kicad_sch]
2026-03-15 Updates on component placements
    [capybara_rocket.kicad_pcb, capybara_rocket.kicad_sch]
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2026-03-23 added dfx files for gnd station base, for lasercutting
    [back_inner.dxf, back_outer.dxf, bottom.dxf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]
2026-03-23 added dfx files for gnd station cover - gs_base renamed folder
    [back.dxf, back_inner.dxf, back_outer.dxf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]
2026-03-25 PCB rearrangement update
    [capybara_rocket.kicad_pcb]
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2026-04-04 Locking in sensor placements
    [capybara_rocket.kicad_pcb, capybara_rocket.kicad_sch]
2026-04-06 Finalized schematic design for CPL and ERC pass
    [capybara_rocket.kicad_pcb, capybara_rocket.kicad_sch]
2026-04-06 New graphics and layout work
    [capybara_rocket.kicad_pcb, capybara_rocket.kicad_sch]
2026-04-09 Completed layout for CPL PCB
    [capybara_rocket.kicad_pcb, capybara_rocket.kicad_sch]
2026-04-09 Left side of the board done :)
    [capybara_rocket.kicad_pcb]
2026-04-10 i used to pray for times like this
    [capybara_rocket.kicad_pcb]
2026-04-10 i used to pray for times like this pt2
    [capybara_rocket.kicad_pcb]
2026-04-11 fixed up board debugging proceedure, and other stuff
2026-04-11 updated board debuging, now correct for seperate power rails
2026-04-13 cpl pcb schematic review complete
    [capybara_rocket.kicad_sch]
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2026-04-15 working on gnd station pcb
    [capybara_habitat.kicad_pcb, capybara_habitat.kicad_sch]
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2026-04-15 gnd station scematic basically done. must fix ERC issues
    [capybara_habitat.kicad_sch]
2026-04-15 Halfway through schematic fixes
    [capybara_rocket.kicad_sch]
2026-04-16 All fixes made on CPL board except inductor change for LTC353:
    [capybara_rocket-B_Cu (Power + Signal).gbr, capybara_rocket-B_Mask.gbr, capybara_rocket-B_Paste.gbr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]
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2026-04-17 V2 of CPL board
    [capybara_rocket.kicad_pcb]
2026-04-17 Gerber files added as well
    [capybara_rocket-B_Cu (Power + Signal).gbr, capybara_rocket-B_Mask.gbr, capybara_rocket-B_Paste.gbr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]
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2026-04-17 Fixed some ERC errors and warnings
    [capybara_habitat.kicad_pcb, capybara_habitat.kicad_sch]
2026-04-17 Updating ERC fixes and KiCad models for the Ground Station PCB
    [capybara_habitat.kicad_pcb, capybara_habitat.kicad_sch]
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2026-04-17 Female DC Barrel Jack footprint added
    [capybara_habitat.kicad_pcb, capybara_habitat.kicad_sch]
2026-04-17 Fixed DC motor trace width
    [capybara_rocket.kicad_pcb]
2026-04-17 Finalize board and gerber files for CPL board
    [capybara_rocket-B_Cu (Power + Signal).gbr, capybara_rocket-B_Mask.gbr, capybara_rocket-B_Paste.gbr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]
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2026-04-23 gnd station schematic bulk complete, need to fix DRC and JST connections
    [capybara_habitat.kicad_pcb, capybara_habitat.kicad_sch]
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2026-04-24 Initial ERC fixes for ground station board
    [capybara_habitat.kicad_pcb, capybara_habitat.kicad_sch]
2026-04-24 Add ERCs fixed for ground station
    [capybara_habitat.kicad_sch]
2026-04-24 Fixed all GND trace issues
    [capybara_habitat.kicad_pcb]
2026-04-25 Adding new silkscreen graphics to ground station board
    [capybara_habitat.kicad_pcb]
2026-04-25 Fixed all DRC issues ground station board
    [capybara_habitat.kicad_pcb]
2026-04-25 Adding .STEP and gerber fab files
    [capybara_habitat-B_Cu (GND).gbr, capybara_habitat-B_Mask.gbr, capybara_habitat-B_Paste.gbr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]
2026-04-25 silk screen edits + power jst
    [capybara_habitat.kicad_pcb, capybara_habitat.kicad_sch]
2026-04-25 Finalizing ground station design
    [capybara_habitat.kicad_pcb]
2026-04-25 Adding new gerber zip for ground station
    [capybara_habitat-B_Cu (GND).gbr, capybara_habitat-B_Mask.gbr, capybara_habitat-B_Paste.gbr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]
2026-04-25 Fixed gerber
    [capybara_habitat-B_Cu (GND).gbr, capybara_habitat-B_Mask.gbr, capybara_habitat-B_Paste.gbr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]
2026-04-25 Fixed cutout on gerber
    [capybara_habitat-B_Cu (GND).gbr, capybara_habitat-B_Mask.gbr, capybara_habitat-B_Paste.gbr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]
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2026-04-26 fix git oopsie + updated gnd station base top - allow more space for pi wires
    [top.dxf]
2026-05-01 working on gnd station lazercut
    [gs_base_inner.dwg]
2026-05-15 added sponsors + top outer side for lazer cutting
    [CompositesCanadaLogo.dxf, ECE_Signature_655.dxf, EngSci_Signature_655.dxf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]
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2026-05-20 ground station dwg sent to myfab
    [gs_top_inner.dwg, gs_top_outer.dwg, left_inner_v2.dxf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]
2026-05-26 fixes to gnd station post production
    [capybara_habitat.kicad_sch]
2026-05-29 added daniels architechure building lazer cutting files cuz myfab cutter broke
    [gs_base_inner.dwg, ils_boundary_1219mm_by_609mm.dwg, pls_boundary_812mm_by_457mm.dwg]
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2026-06-02 Moving other folder into dedicated ground_station folder
    [cansat_data.csv, pyvenv.cfg, telemetry_data.csv]
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
